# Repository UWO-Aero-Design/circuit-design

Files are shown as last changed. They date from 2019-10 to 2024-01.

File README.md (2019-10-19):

# WE Aero Design Onboard Hardware

## Goal
The hardware soloution will contain sensors that allow the team to accurately determine the height and position of the aircraft at any given moment. Also, the system should allow for communication with the ground station through an onboard radio. Logging of in-flight data and accurate GPS information will be necessary. Finally, the system must be able to control 16 individual servos or DC motors.

## Design
Below are screenshots of the current revision of the schematic and board (created in Eagle).

### Schematic
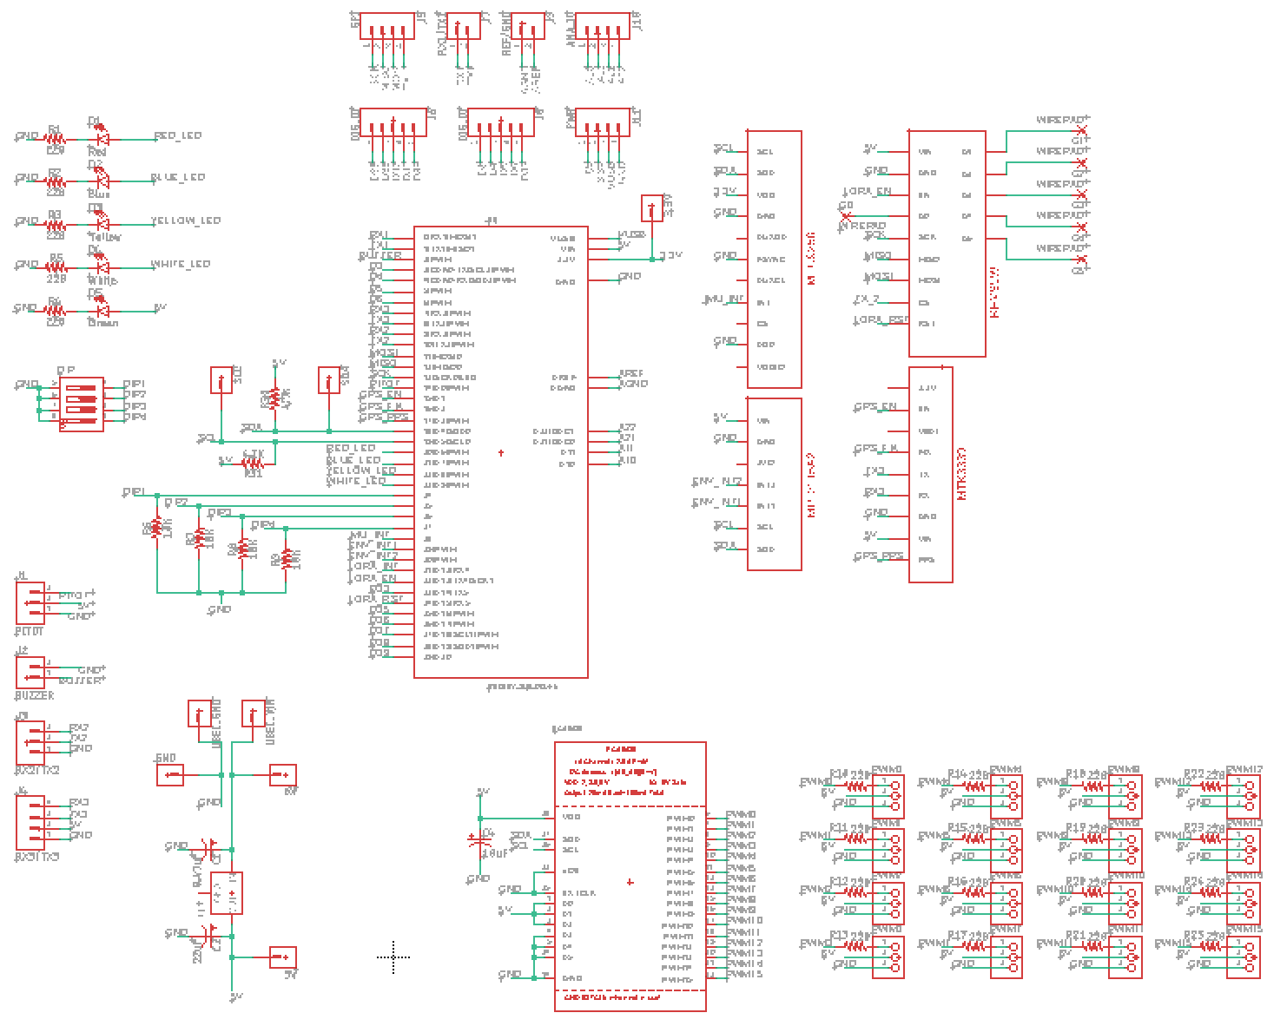
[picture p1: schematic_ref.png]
Schematic

### Board
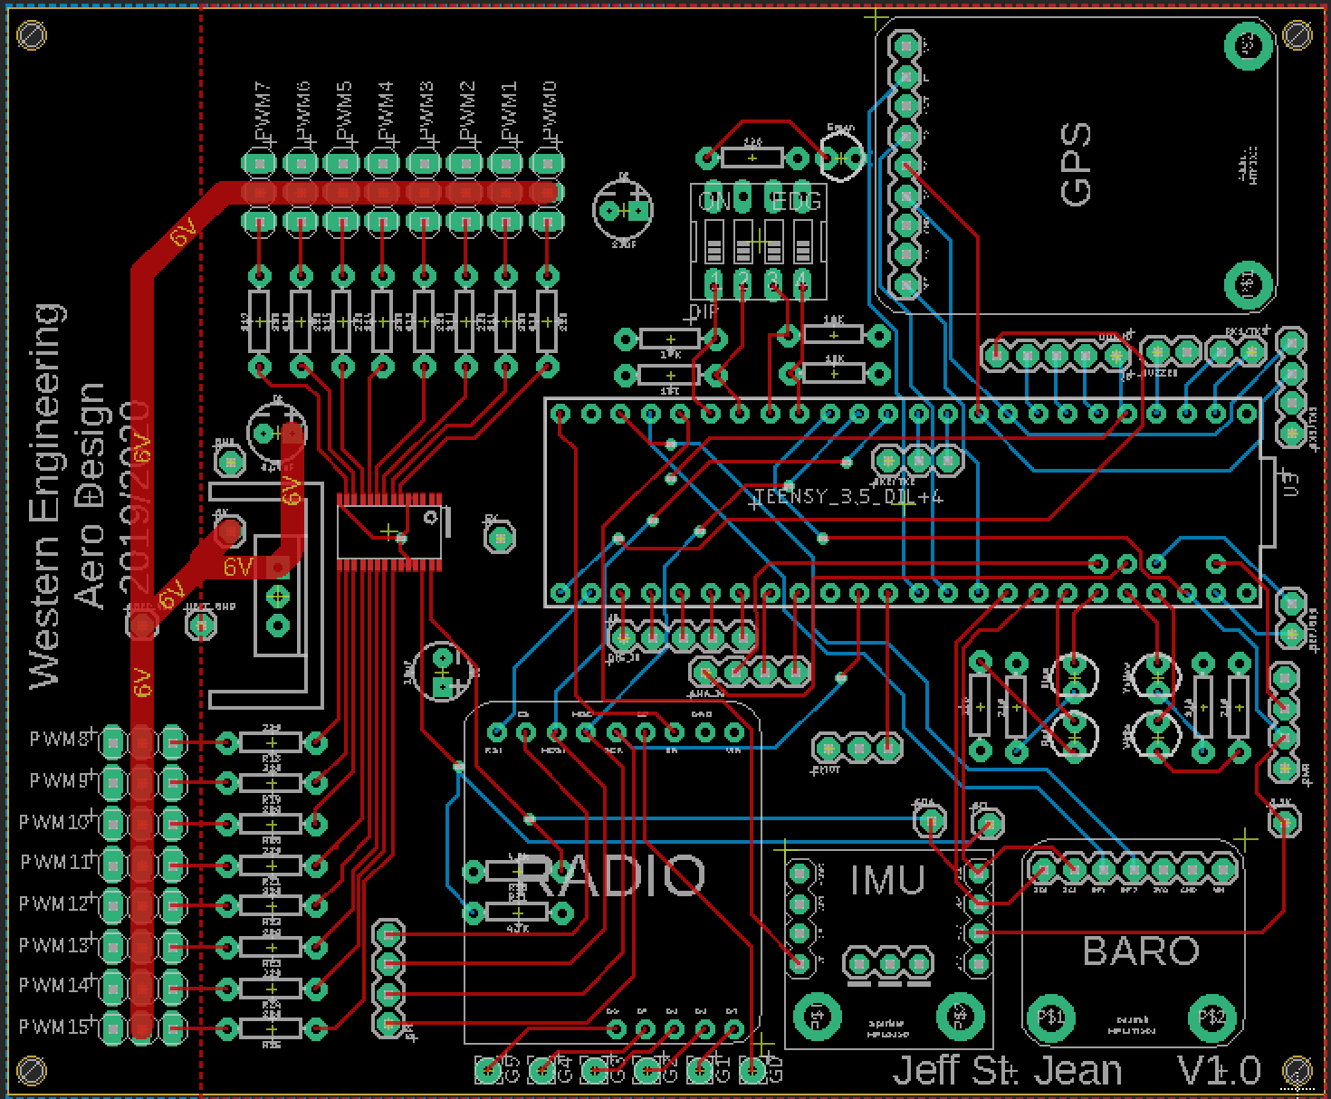
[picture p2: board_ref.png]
board


## Features
#### Radio
[RFM95W](https://www.adafruit.com/product/3072)

#### IMU
[MPU9250](https://www.sparkfun.com/products/13762)

#### Evironment Sensing
[MPL3115A2](https://www.adafruit.com/product/1893)

#### GPS
[Adafruit Ultimate GPS Breakout](https://www.adafruit.com/product/746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)

#### Servo Driver
[PCA9686](https://cdn-shop.adafruit.com/datasheets/PCA9685.pdf)

#### Power
[L7805 and L7806](https://www.mouser.ca/datasheet/2/389/l78m-974157.pdf)

## TODO
- [x] Select parts
- [x] Create schematic
- [x] Layout board
- [x] Route board
- [x] Order board
- [ ] Test board

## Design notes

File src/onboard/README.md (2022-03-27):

# WE Aero Design Onboard Hardware

## Goal
The hardware soloution will contain sensors that allow the team to accurately determine the height and position of the aircraft at any given moment. Also, the system should allow for communication with the ground station through an onboard radio. Logging of in-flight data and accurate GPS information will be necessary. Finally, the system must be able to control 16 individual servos or DC motors.

The team would also like to implement flight stabilization by activating a secondary Teensy which would control four servos attached to control surfaces: 2 aileron, 1 rudder, and 1 elevator. Activation of the secondary Teensy will be done by the Main Teensy. 

## Design
Below are screenshots of the current revision of the schematic and board of the Navigation and Main Teensy (created in Eagle).

### Schematic of Main Teensy
Schematic of Main Teensy
### Board of Main Teensy
Board of Main Teensy

### Schematic of Navigation Teensy
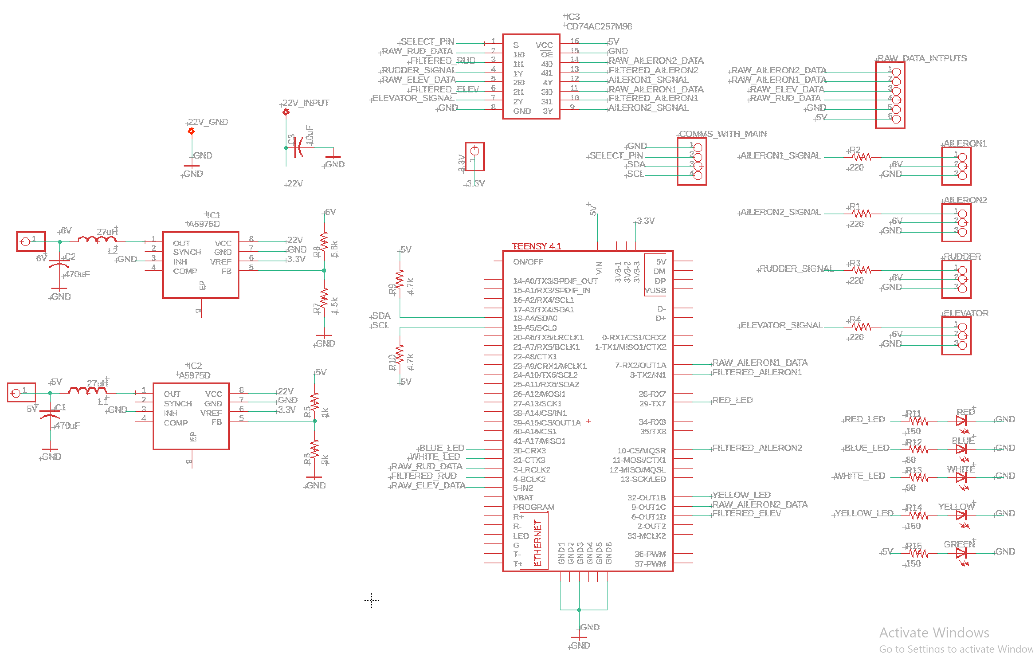
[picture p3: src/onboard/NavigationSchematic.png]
Schematic of Navigation Teensy

### Board of Navigation Teensy
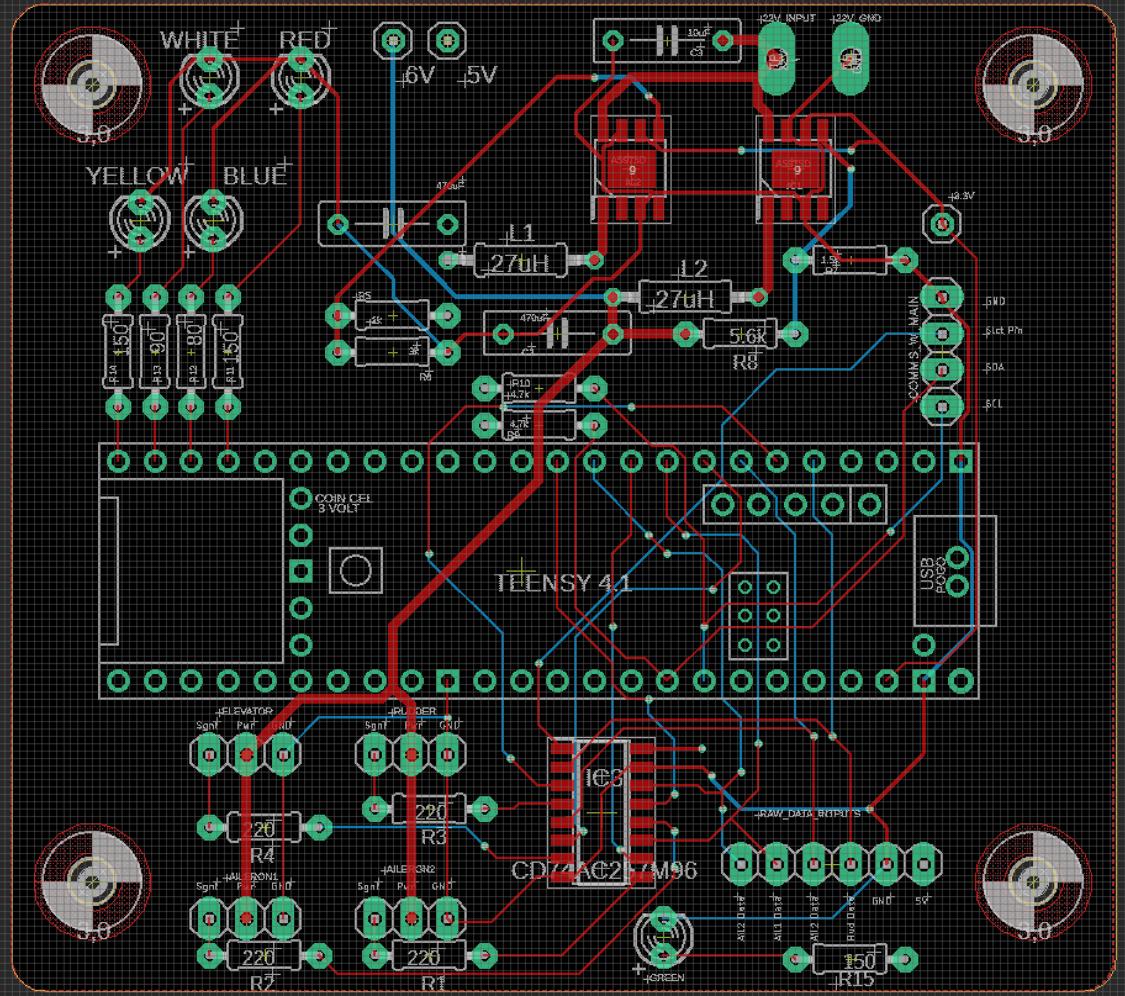
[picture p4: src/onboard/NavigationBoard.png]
Board of Navigation Teensy


## Features
#### Teensy
[Teensy 4.1](https://www.digikey.ca/en/products/detail/sparkfun-electronics/DEV-16996/13158152)

#### Radio
[RFM95W](https://www.adafruit.com/product/3072)

#### IMU
[ICM20948](https://www.digikey.ca/en/products/detail/pimoroni-ltd/PIM448/10246391)

#### Environment Sensing
[BMP280](https://www.digikey.ca/en/products/detail/adafruit-industries-llc/2651/5604371)

#### Pitot Tube
[Pitot Tube-MPXV7002DP](https://www.digikey.ca/en/products/detail/nxp-usa-inc/MPXV7002DP/1168436)

#### GPS
[Adafruit Ultimate GPS Breakout](https://www.digikey.ca/en/products/detail/adafruit-industries-llc/746/5353613)

#### Servo Driver
[PCA9685PW,112](https://www.digikey.ca/en/products/detail/nxp-usa-inc/PCA9685PW112/2034324)

#### Multiplexer
[CD74AC257M96](https://www.digikey.ca/en/products/detail/texas-instruments/CD74AC257M96/1691832)

#### Power
[A5975D](https://www.digikey.ca/en/products/detail/stmicroelectronics/A5975D/4357599)

## TODO
- [x] Select parts
- [x] Create schematic
- [x] Layout board
- [x] Route board
- [ ] Order board
- [ ] Test board

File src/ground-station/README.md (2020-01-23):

# WE Aero Design Ground Station Utility Hardware

## Goal
The hardware contains a radio and bluetooth module to allow communications between the plane's onboard system and the groundstation web server. It also contains an OLED screen to display basic information to the user as data is sent and recieved.  

## Design
Below are screenshots of the current revision of the schematic and board (created in Eagle).

### Schematic
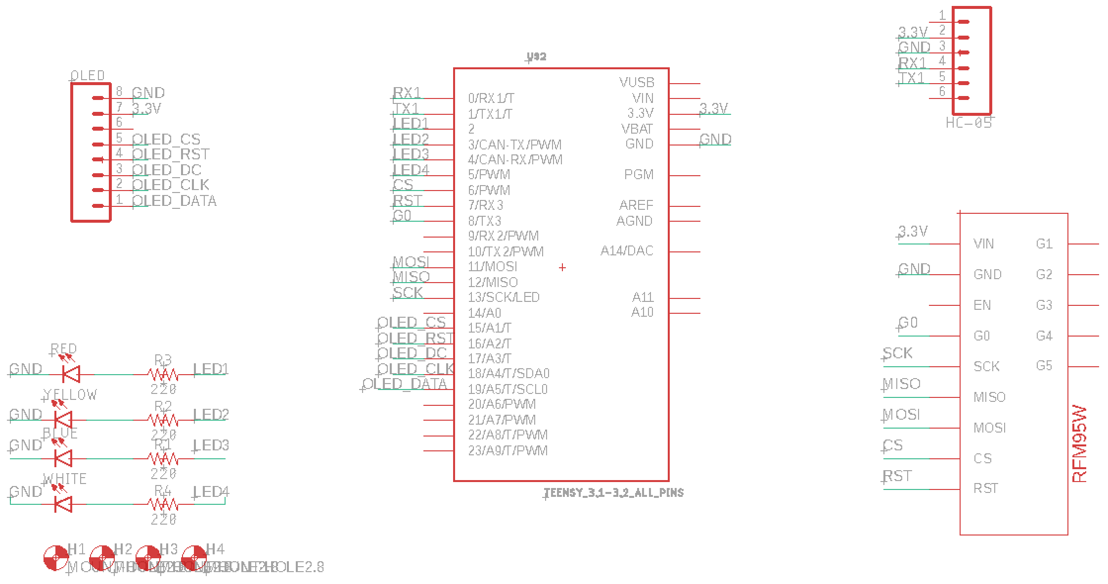
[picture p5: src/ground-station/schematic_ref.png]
Schematic

### Board
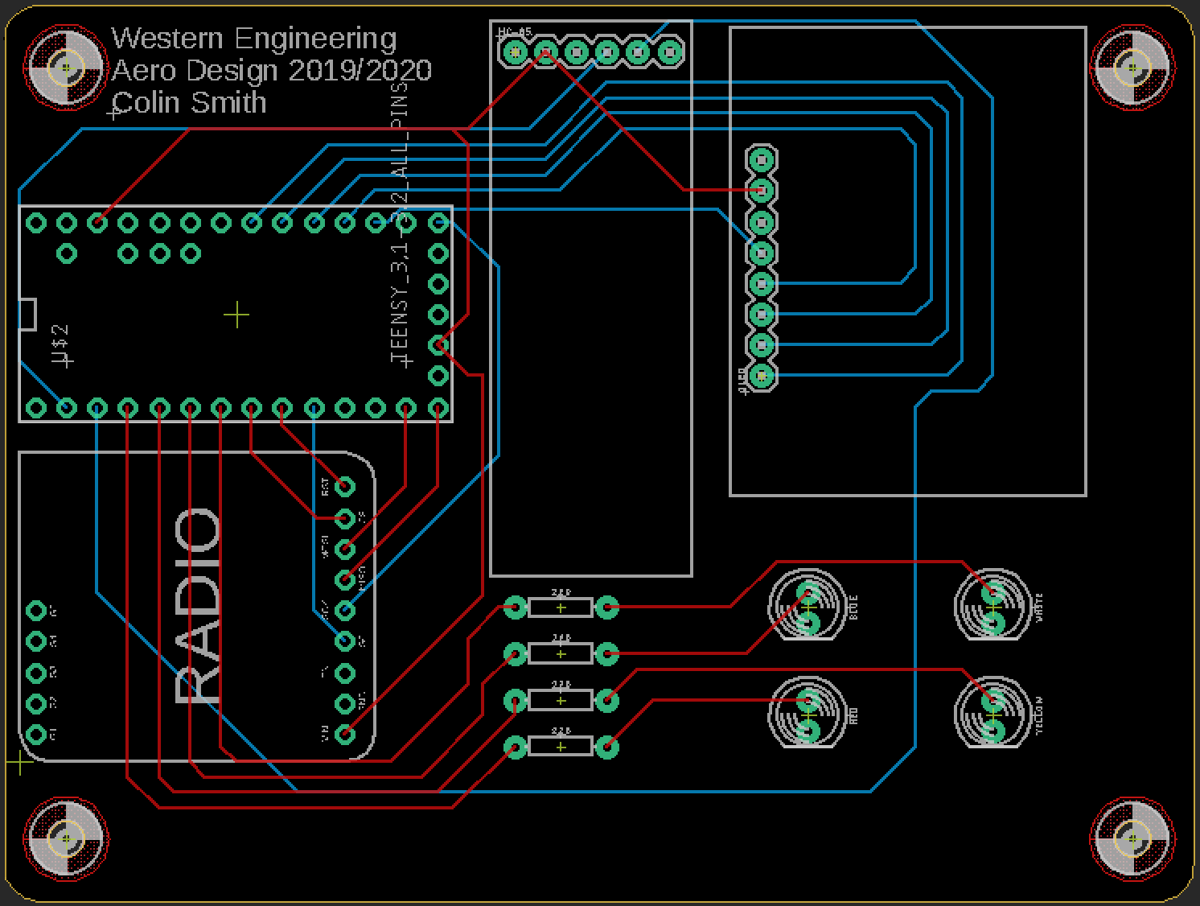
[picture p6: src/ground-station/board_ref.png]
board


## Features
#### Radio
[RFM95W](https://www.adafruit.com/product/3072)

#### Bluetooth
[HC-05](https://components101.com/wireless/hc-05-bluetooth-module)

#### OLED
[128x64 OLED](https://www.adafruit.com/product/326)

## TODO
- [x] Create schematic
- [x] Solder board
- [ ] Test Board

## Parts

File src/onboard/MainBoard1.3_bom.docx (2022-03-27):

Component | Quantity Used
Buck Converter | 3
Teensy 4.1 | 1
GPS | 1
Servo Driver | 1
Radio | 1
IMU | 1
Pitot Tube | 1
Barometer | 1
Female Header | 144
27uH Inductor | 3
470uF Capacitor | 3
10uF Capacitor | 4
1.8M Resistor | 1
430k Resistor | 1
2.2k Resistor | 5
150 Resistor | 4
80 Resistor | 1
90 Resistor | 1
5.6k Resistor | 2
1.5k Resistor | 2
1k Resistor | 1
3k Resistor | 1
10k Resistor | 2
4.7k Resistor | 2
4.3k Resistor | 1
220 Resistor | 16
ORANGE LED | 1
WHITE LED | 1
YELLOW LED | 1
RED LED | 1
BLUE | 1
GREEN LED | 1
4 DIP Switch | 1
M3 Screws | 4

Main Board:

Navigation Board:

Component | Quantity Used
Teensy 4.1 | 1
Mux | 1
Buck Converter | 2
Servo Driver | 1
27uH Inductor | 2
470uF Capacitor | 2
10uF Capacitor | 1
5.6k Resistor | 1
1.5k Resistor | 1
1k Resistor | 1
3k Resistor | 1
4.7k Resistor | 2
220 Resistor | 4
150 Resistor | 3
80 Resistor | 1
90 Resistor | 1
RED LED | 1
BLUE LED | 1
GREEN LED | 1
WHITE LED | 1
YELLOW LED | 1
Female Headers | 37
M3 Screws | 4

Component | Link | Price/1
Buck Converter | https://www.digikey.ca/en/products/detail/stmicroelectronics/A5975D/4357599 | 6.76 $
MUX | https://www.digikey.ca/en/products/detail/texas-instruments/CD74AC257M96/1691832 | 1.50 $
Teensy 4.1 | https://www.pjrc.com/store/teensy41.html | 26.85 $
GPS | https://www.digikey.ca/en/products/detail/adafruit-industries-llc/746/5353613 | 54.27 $
Radio | https://www.digikey.ca/en/products/detail/adafruit-industries-llc/3073/6005358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 | 27.10 $
Servo Driver | https://www.digikey.ca/en/products/detail/nxp-usa-inc/PCA9685PW112/2034324 | 3.47 $
IMU | https://www.digikey.ca/en/products/detail/pimoroni-ltd/PIM448/10246391 | 20.38 $
Pitot Tube | https://www.digikey.ca/en/products/detail/nxp-usa-inc/MPXV7002DP/1168436 | 27.44 $
Barometer | https://www.digikey.ca/en/products/detail/adafruit-industries-llc/2651/5604371 | 13.52 $
Header | https://www.digikey.ca/en/products/detail/sullins-connector-solutions/PPTC361LFBN-RC/810173 | 2.80 $
DIP Switches | https://www.digikey.ca/en/products/detail/grayhill-inc/76SB04T/726228 | 1.52 $
Inductors | https://www.digikey.ca/en/products/detail/epcos-tdk-electronics/B78108S1474J000/652558 | 0.50 $
Capacitors (Box) | https://www.amazon.ca/Ceramic-Capacitor-Electrolytic-Portable-Assortment/dp/B082F37H38 | 42.99 $
Resistors | https://www.digikey.ca/en/products/detail/koa-speer-electronics-inc/CF1-4CT52R104J/13537243 | 0.14 $
LEDs (Box) | https://www.amazon.ca/DiCUNO-450pcs-Colors-Emitting-Assorted/dp/B073QMYKDM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 | 19.99 $
Screws | https://www.digikey.ca/en/products/detail/keystone-electronics/29344/1532217 | 0.32 $

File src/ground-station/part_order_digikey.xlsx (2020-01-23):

Type | Qty | Device | Value | Link
Resistors | 4 | 330OHM-HORIZ-1/10W-5% | 220 | https://www.digikey.ca/product-detail/en/stackpole-electronics-inc/CF14JT220R/CF14JT220RTR-ND/1741346
Peripherals | 1 | TEENSY_3.2 | TEENSY_3.2 | https://www.digikey.ca/product-detail/en/sparkfun-electronics/DEV-13736/1568-1231-ND/5721426
 | 1 | OLED Screen | 128x64 | https://www.digikey.ca/product-detail/en/adafruit-industries-llc/326/1528-1220-ND/5353680
 | 1 | Bluetooth Module | HC-05
Connectors | 55 | Female Headers | 2.54mm Pitch | https://www.digikey.com/product-detail/en/sullins-connector-solutions/PPTC241LFBN-RC/S7022-ND/810162
 | 6 | Right-Angle Male Headers | 2.54mm Pitch | https://www.digikey.ca/product-detail/en/sullins-connector-solutions/PPPC061LGBN-RC/S5481-ND/775939
LEDs | 1 | LED3MM | Yellow LED | https://www.digikey.com/product-detail/en/lumex-opto-components-inc/SSL-LX5093YT/67-1117-ND/270915
 | 1 | LED3MM | Blue LED | https://www.digikey.com/product-detail/en/lumex-opto-components-inc/SSL-LX5093USBD/67-1751-ND/468025
 | 1 | LED3MM | Green LED | https://www.digikey.com/product-detail/en/lumex-opto-components-inc/SSL-LX5093LGT/67-1109-ND/270907
 | 1 | LED3MM | Red LED | https://www.digikey.com/product-detail/en/lumex-opto-components-inc/SSL-LX5093SRD-D/67-1648-ND/413799

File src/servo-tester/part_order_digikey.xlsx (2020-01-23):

Type | Qty | Device | Value | Link
Capacitors | 3 | 10UF-POLAR-RADIAL-2.5MM-25V-20% | 0.1uF | https://www.digikey.com/product-detail/en/vishay-bc-components/K104K15X7RF5TL2/BC1084CT-ND/286706
Resistors | 7 | 330OHM-HORIZ-1/10W-5% | 10K | https://www.digikey.ca/product-detail/en/stackpole-electronics-inc/CF14JT10K0/CF14JT10K0CT-ND/1830374
 | 3 | 330OHM-HORIZ-1/10W-5% | 220 | https://www.digikey.ca/product-detail/en/stackpole-electronics-inc/CF14JT220R/CF14JT220RTR-ND/1741346
Peripherals | 1 | TEENSY_3.2 | TEENSY_3.2 | https://www.digikey.ca/product-detail/en/sparkfun-electronics/DEV-13736/1568-1231-ND/5721426
LEDs | 1 | RGB LED 5MM | RGB LED 5MM | https://www.digikey.ca/product-detail/en/kingbright/WP154A4SUREQBFZGW/754-1492-ND/2261457
Connectors | 58 | Female Headers | 2.54mm Pitch | https://www.digikey.com/product-detail/en/sullins-connector-solutions/PPTC241LFBN-RC/S7022-ND/810162
 | 45 | Male Headers | 2.54mm Pitch | https://www.digikey.ca/product-detail/en/wurth-electronics-inc/61302411121/732-5331-ND/4846867

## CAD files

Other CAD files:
src/ground-station/dhruv_electronic design.f3z

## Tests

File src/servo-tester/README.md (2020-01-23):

# WE Aero Design Servo Tester Hardware

## Goal
To have an easy and portable way to find the bounds of the servos used to actuate the drop mechanism.

## Design
Below are screenshots of the current revision of the schematic and board (created in Eagle).

### Schematic
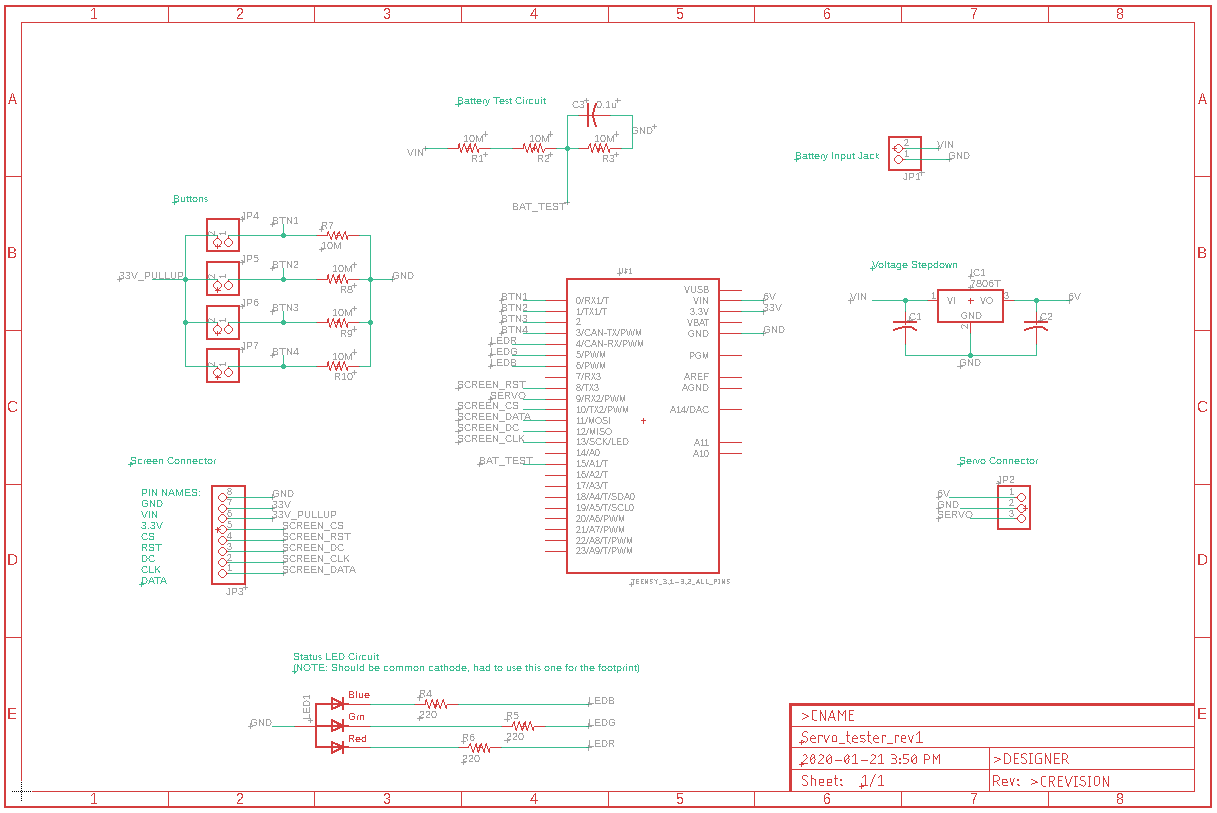
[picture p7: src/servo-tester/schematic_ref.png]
Schematic

### Board
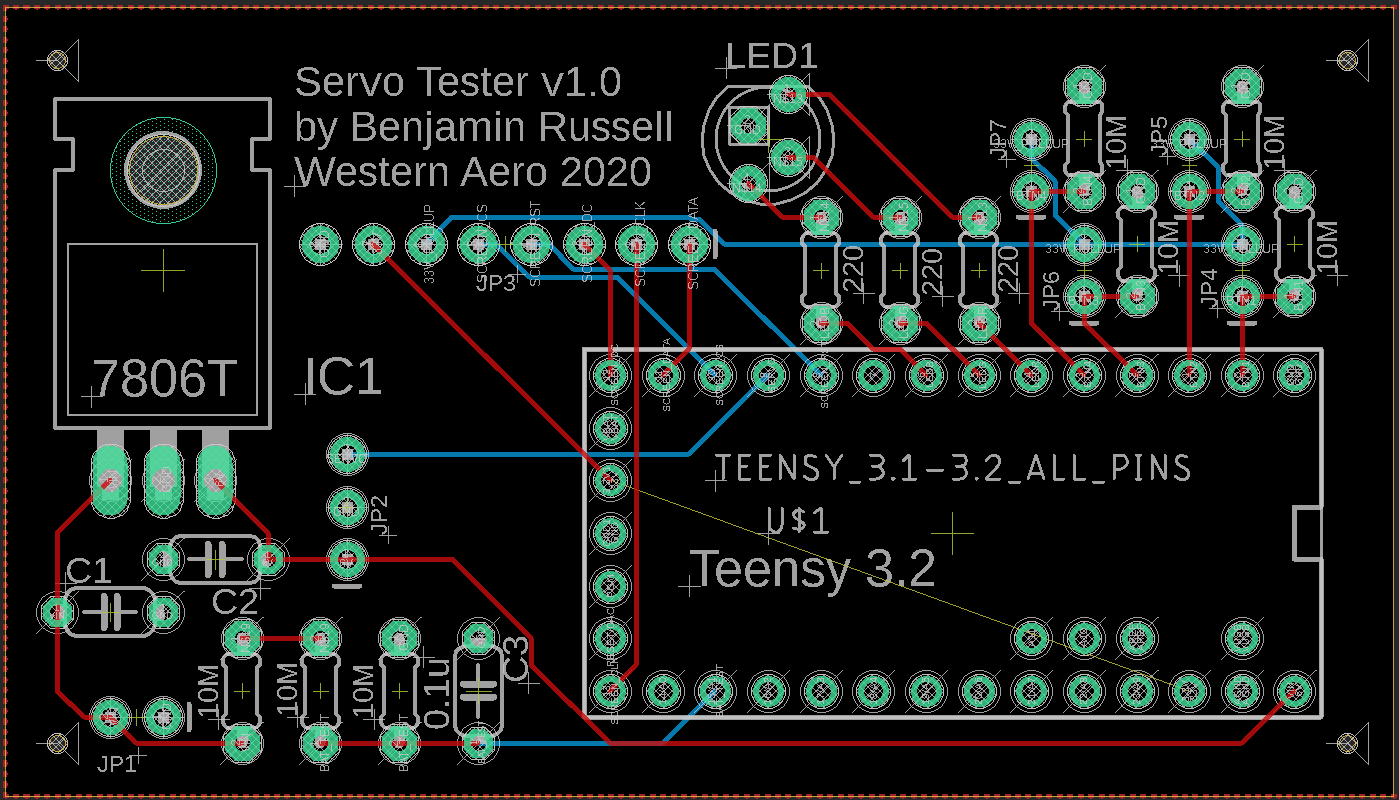
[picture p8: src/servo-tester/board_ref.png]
board


## Features
0.96" High contrast OLED display  
Battery monitor circuit  
Easily replaceable 9v battery, expected 2-4 hour life

## TODO
- [x] Create schematic
- [ ] Solder board
- [ ] Write code
- [ ] Build case

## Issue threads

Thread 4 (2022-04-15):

BMP280 silkscreen is too small

jeffstjean, 2022-04-15:

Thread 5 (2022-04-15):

Silkscreen for 27uH inductor for buck converter is too small

jeffstjean, 2022-04-15:

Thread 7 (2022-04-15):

Silkscreen for 470uF capacitor for buck converter is too small

jeffstjean, 2022-04-15:

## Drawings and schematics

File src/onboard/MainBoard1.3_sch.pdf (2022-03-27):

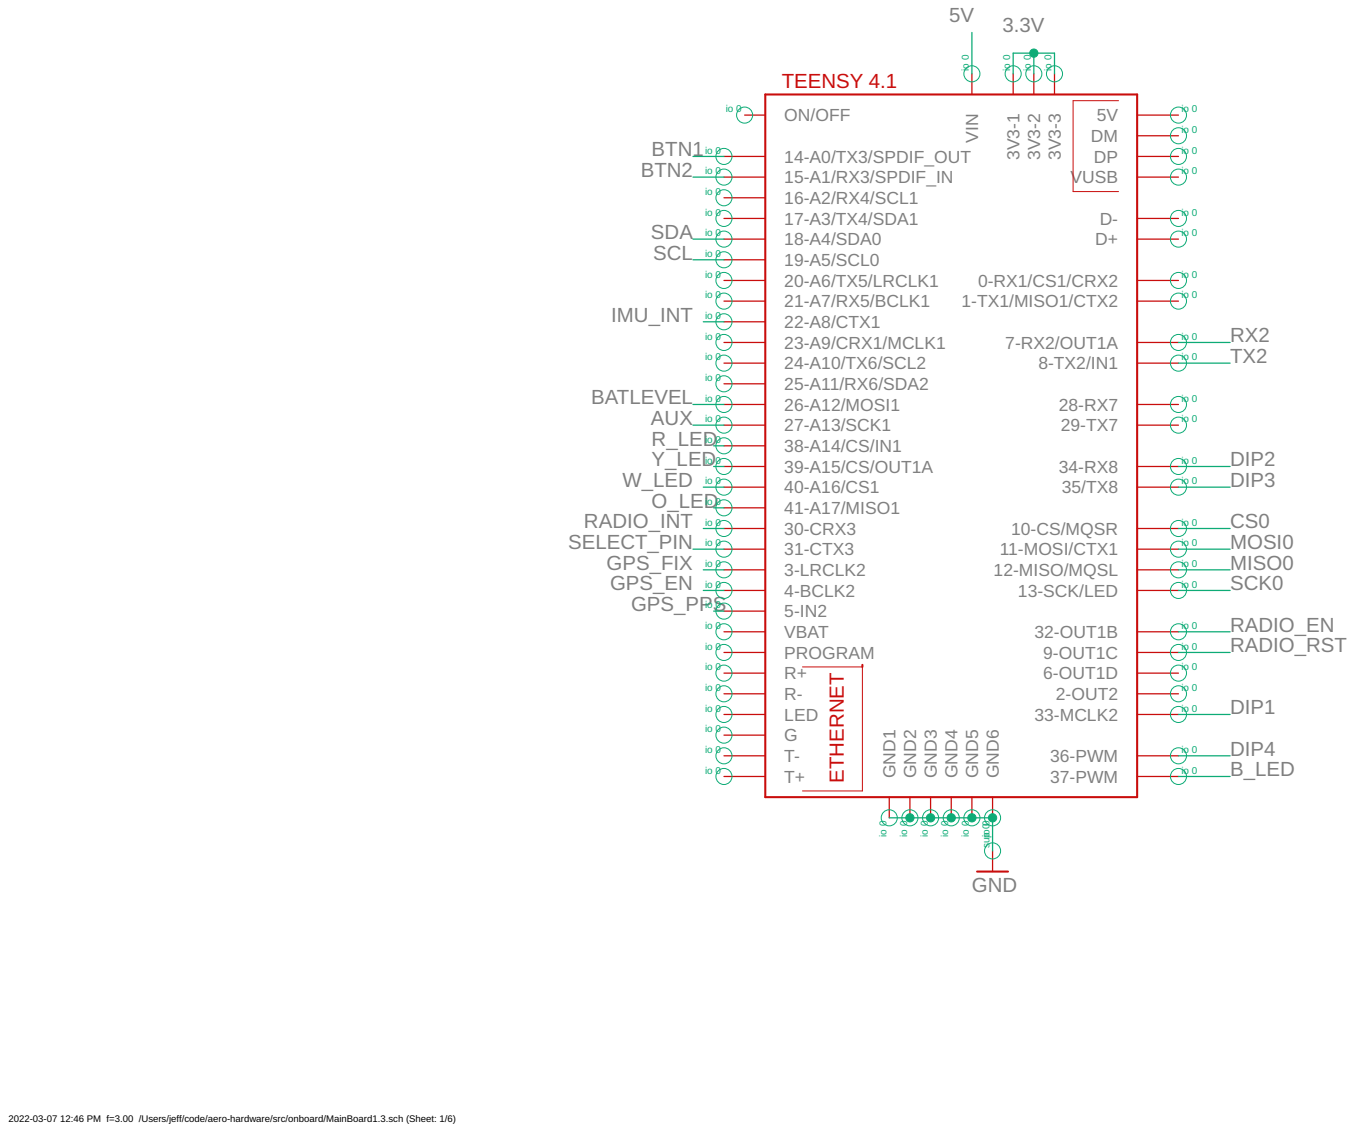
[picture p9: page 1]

2022-03-07 12:46 PM f=3.00 /Users/jeff/code/aero-hardware/src/onboard/MainBoard1.3.sch (Sheet: 1/6)

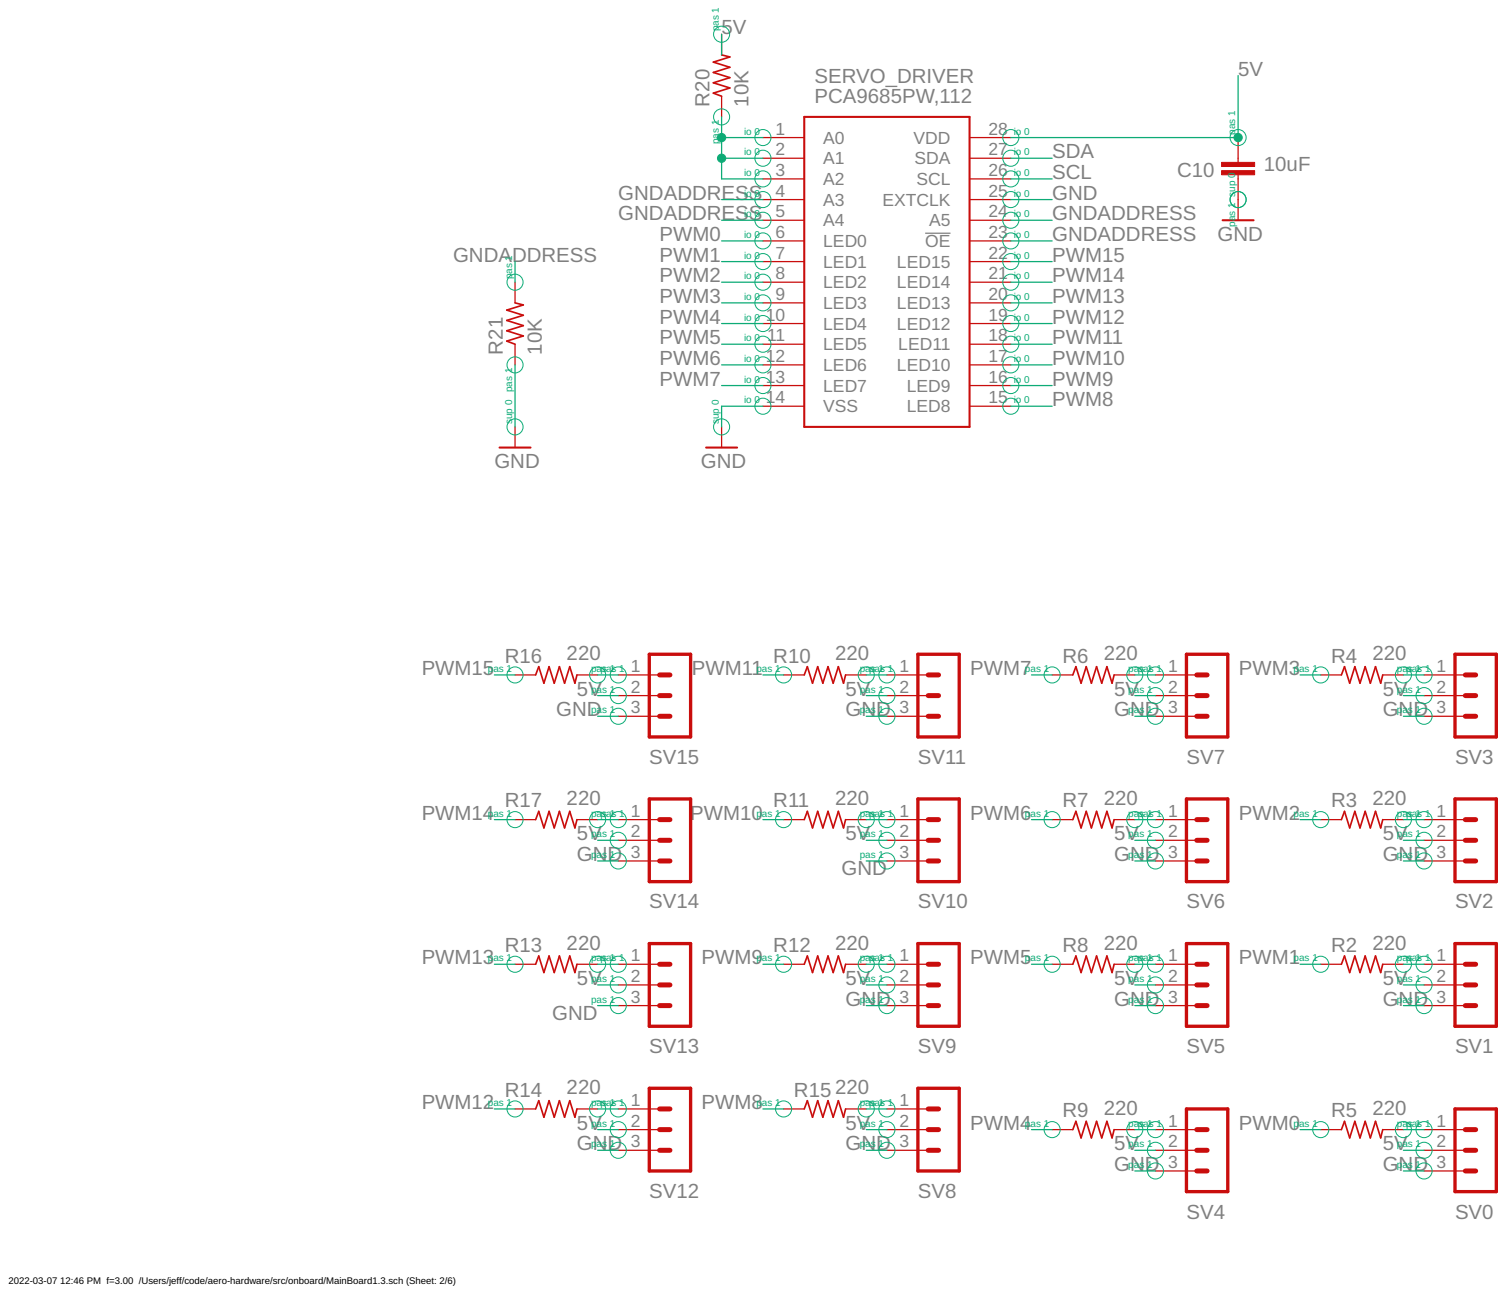
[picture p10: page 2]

2022-03-07 12:46 PM f=3.00 /Users/jeff/code/aero-hardware/src/onboard/MainBoard1.3.sch (Sheet: 2/6)

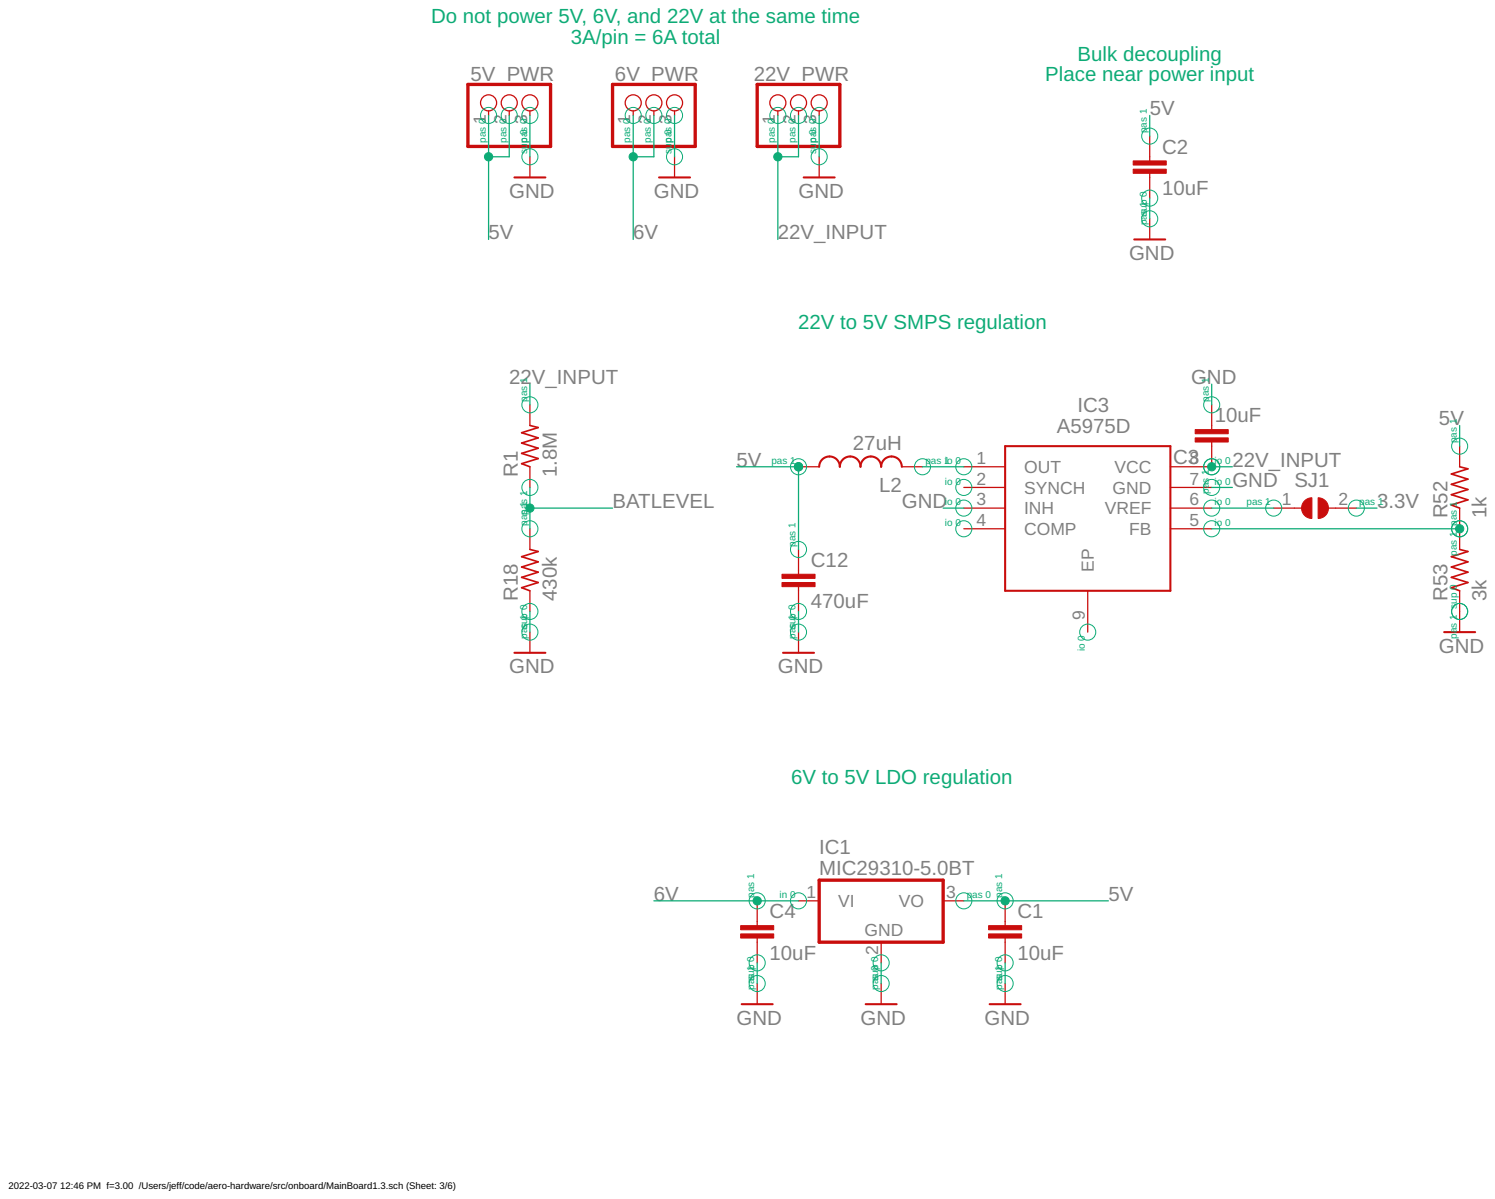
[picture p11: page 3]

Do not power 5V, 6V, and 22V at the same time

Bulk decoupling
Place near power input

2022-03-07 12:46 PM f=3.00 /Users/jeff/code/aero-hardware/src/onboard/MainBoard1.3.sch (Sheet: 3/6)

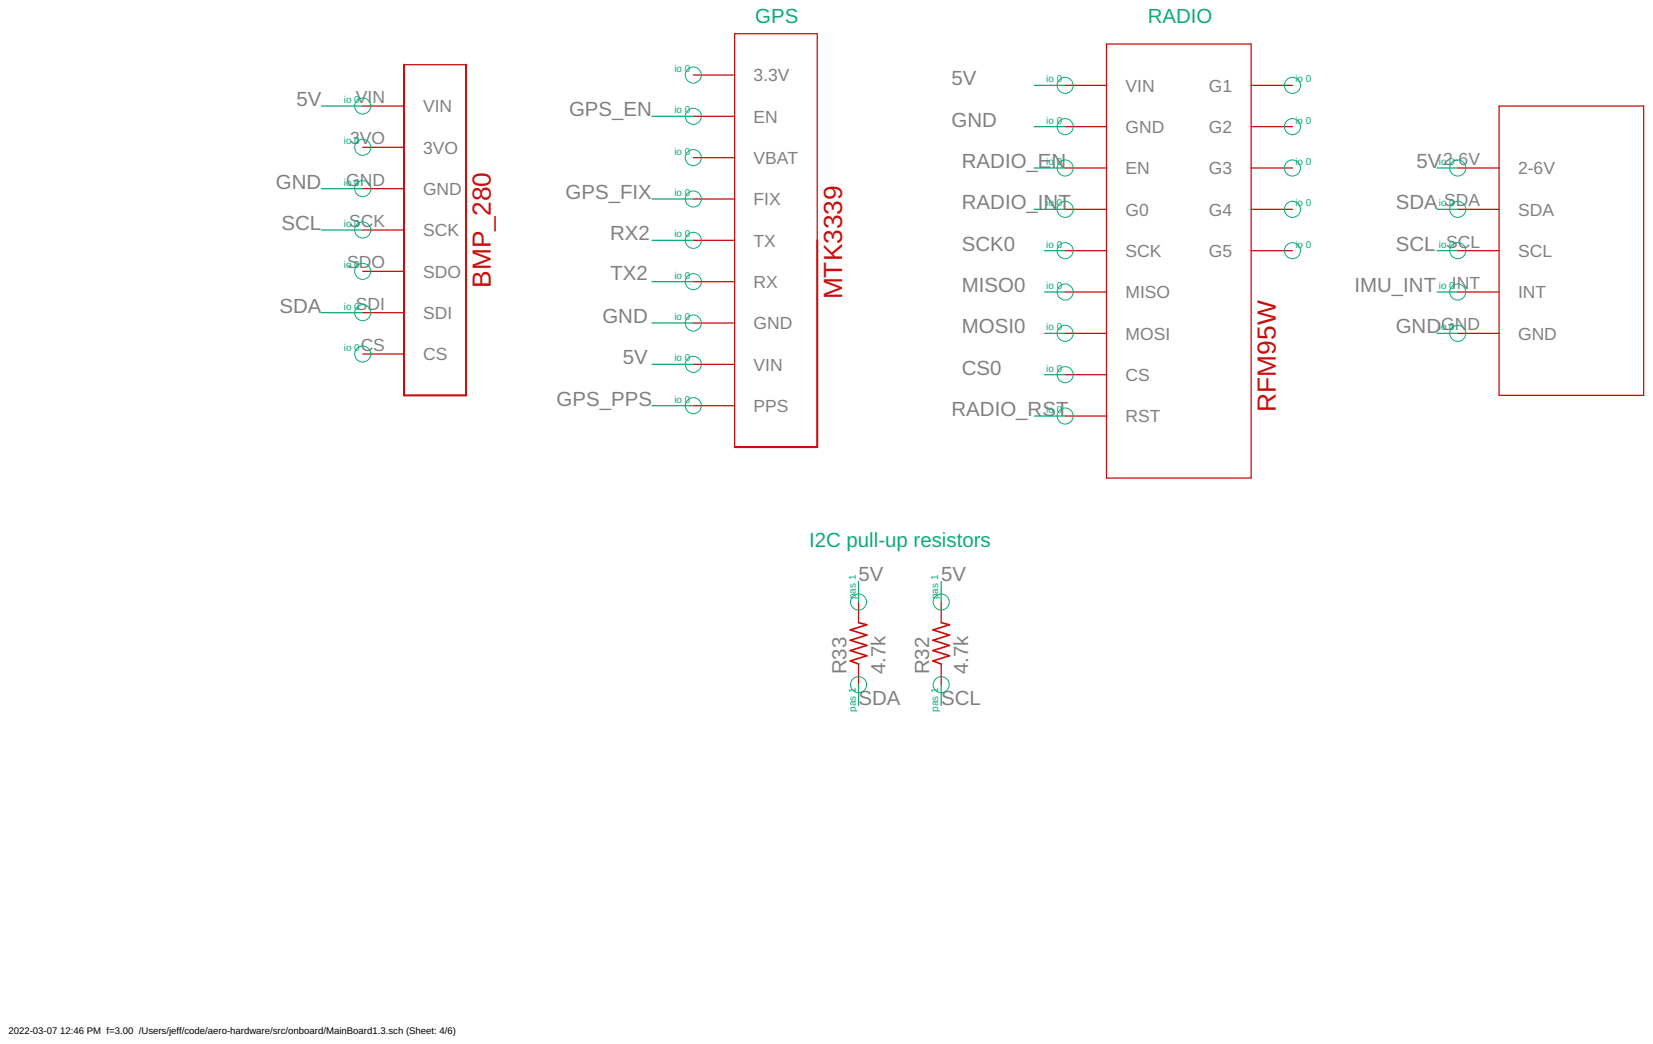
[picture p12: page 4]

2022-03-07 12:46 PM f=3.00 /Users/jeff/code/aero-hardware/src/onboard/MainBoard1.3.sch (Sheet: 4/6)

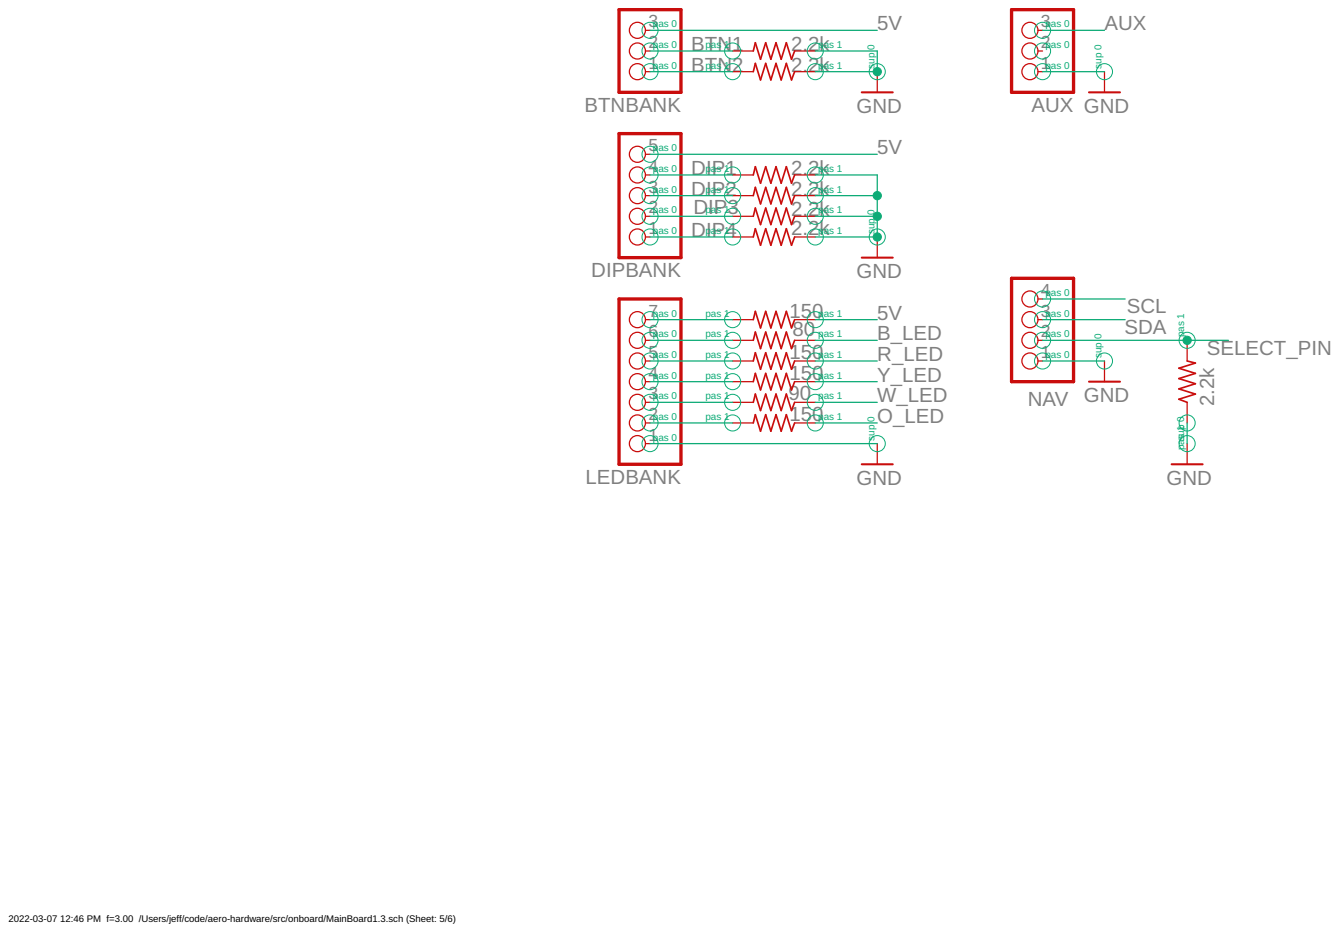
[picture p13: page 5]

2022-03-07 12:46 PM f=3.00 /Users/jeff/code/aero-hardware/src/onboard/MainBoard1.3.sch (Sheet: 5/6)

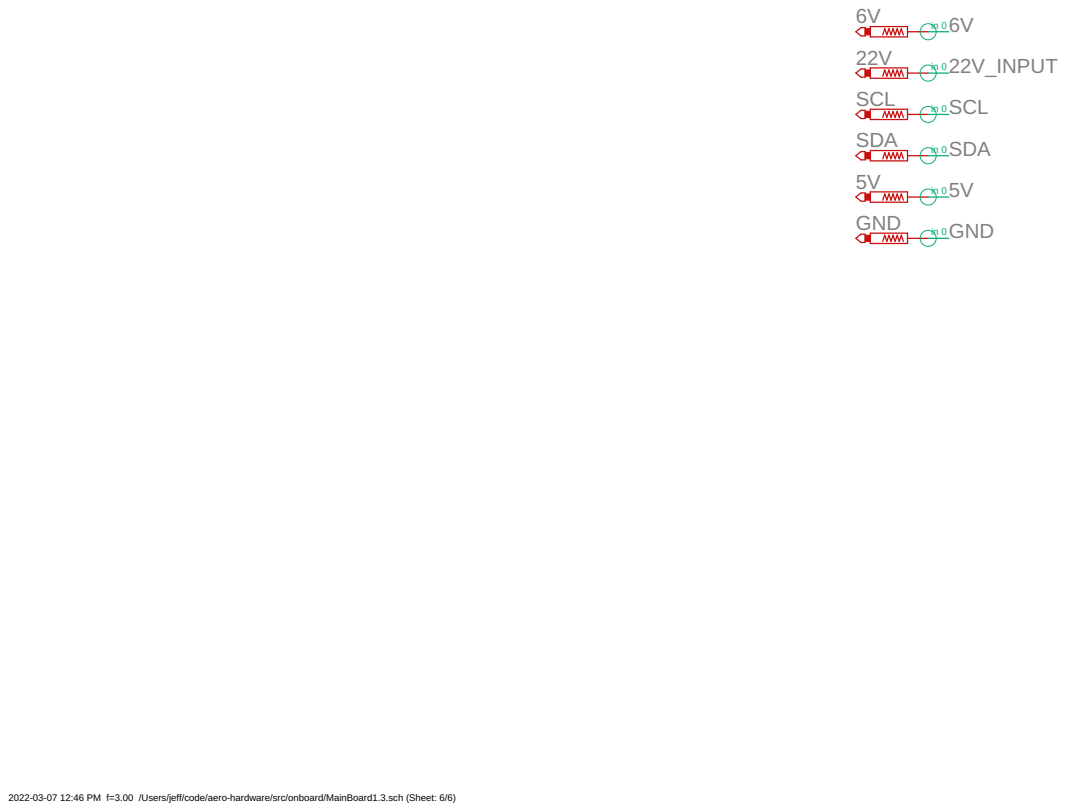
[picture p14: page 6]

2022-03-07 12:46 PM f=3.00 /Users/jeff/code/aero-hardware/src/onboard/MainBoard1.3.sch (Sheet: 6/6)

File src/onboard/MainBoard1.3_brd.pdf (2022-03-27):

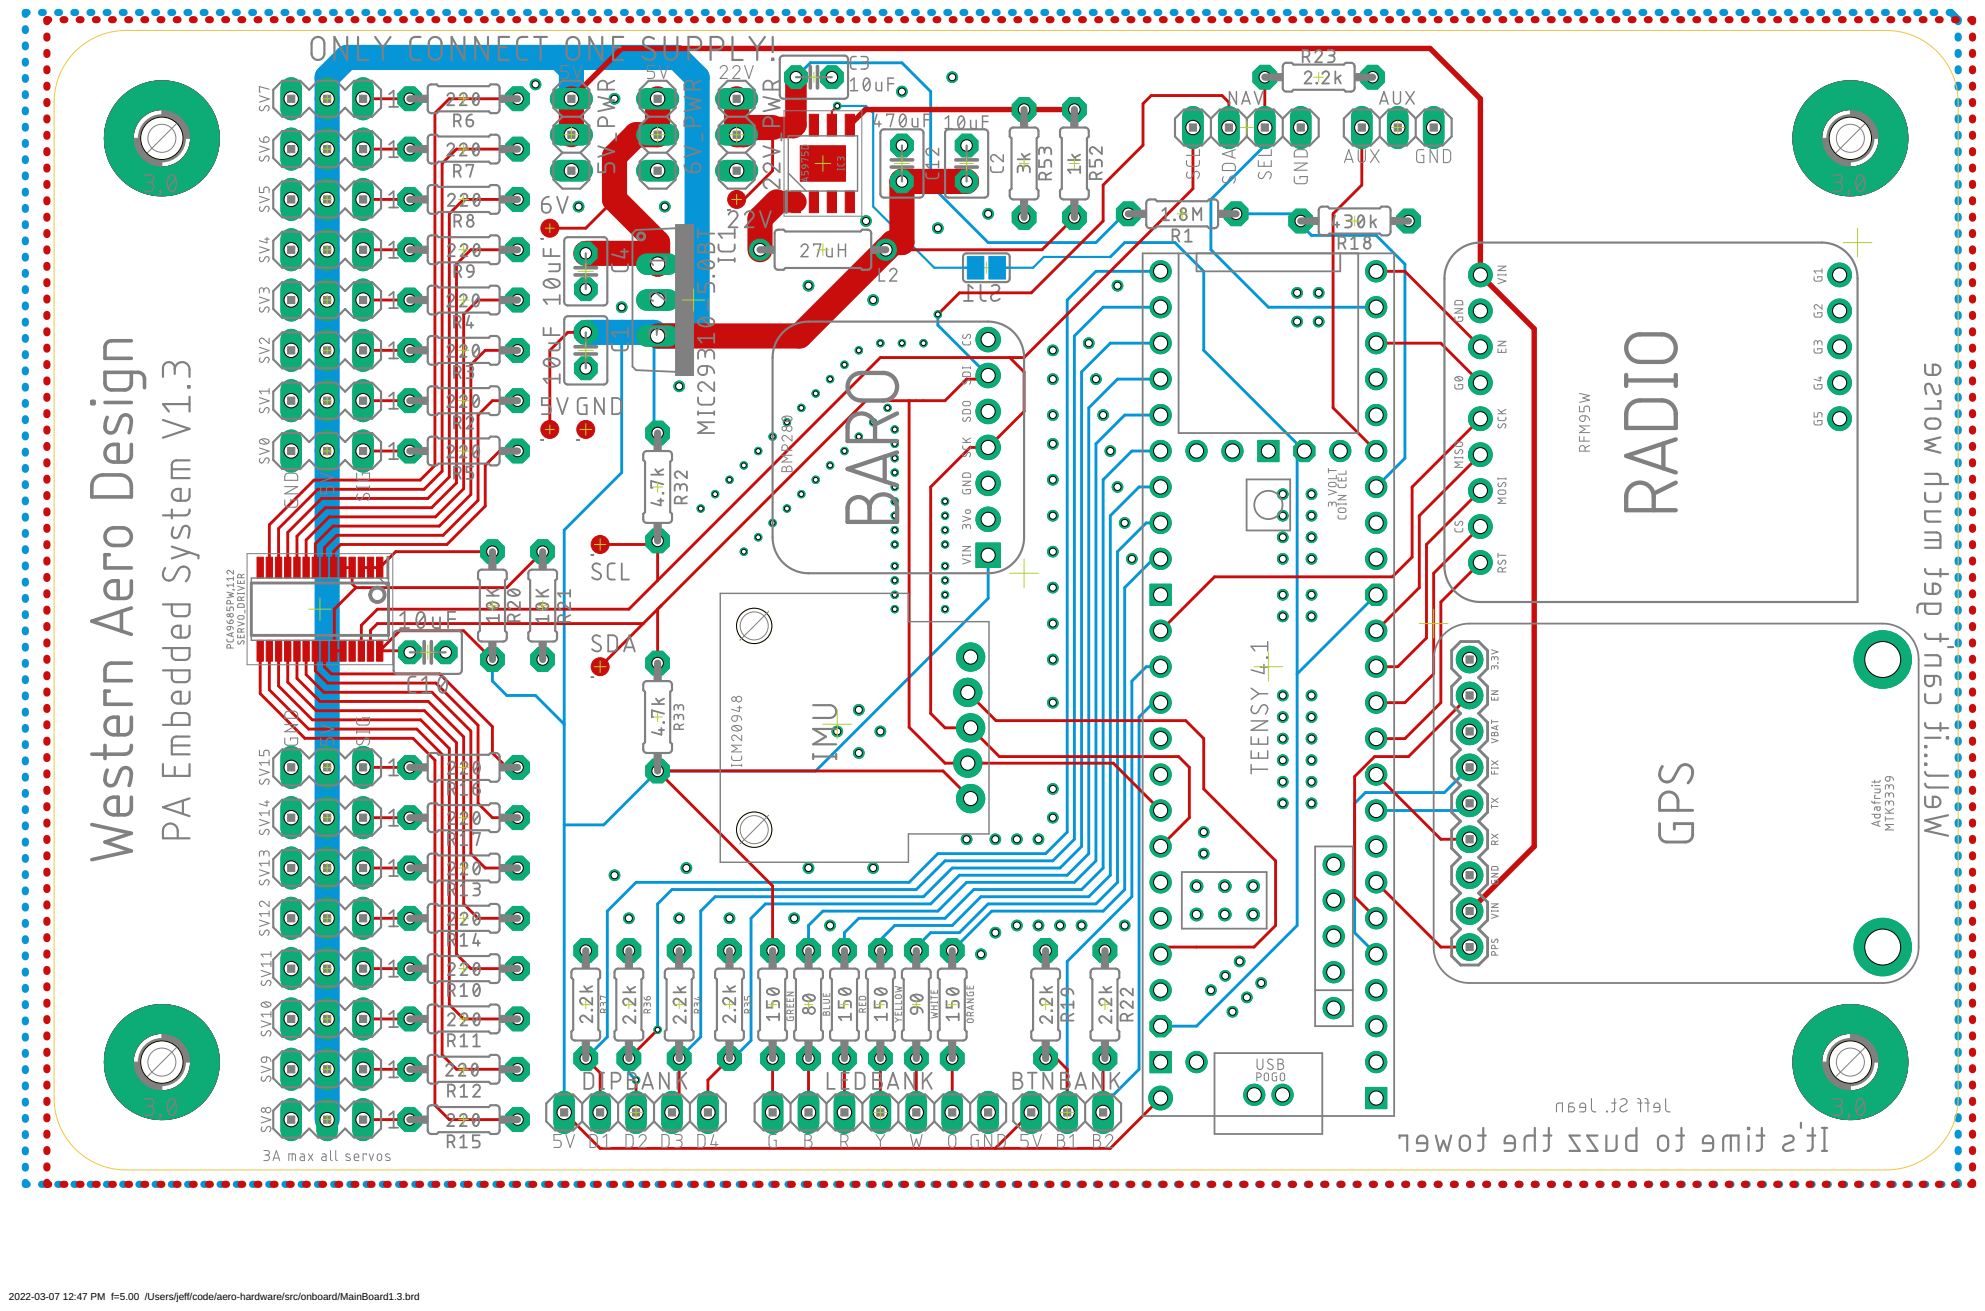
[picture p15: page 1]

2022-03-07 12:47 PM f=5.00 /Users/jeff/code/aero-hardware/src/onboard/MainBoard1.3.brd

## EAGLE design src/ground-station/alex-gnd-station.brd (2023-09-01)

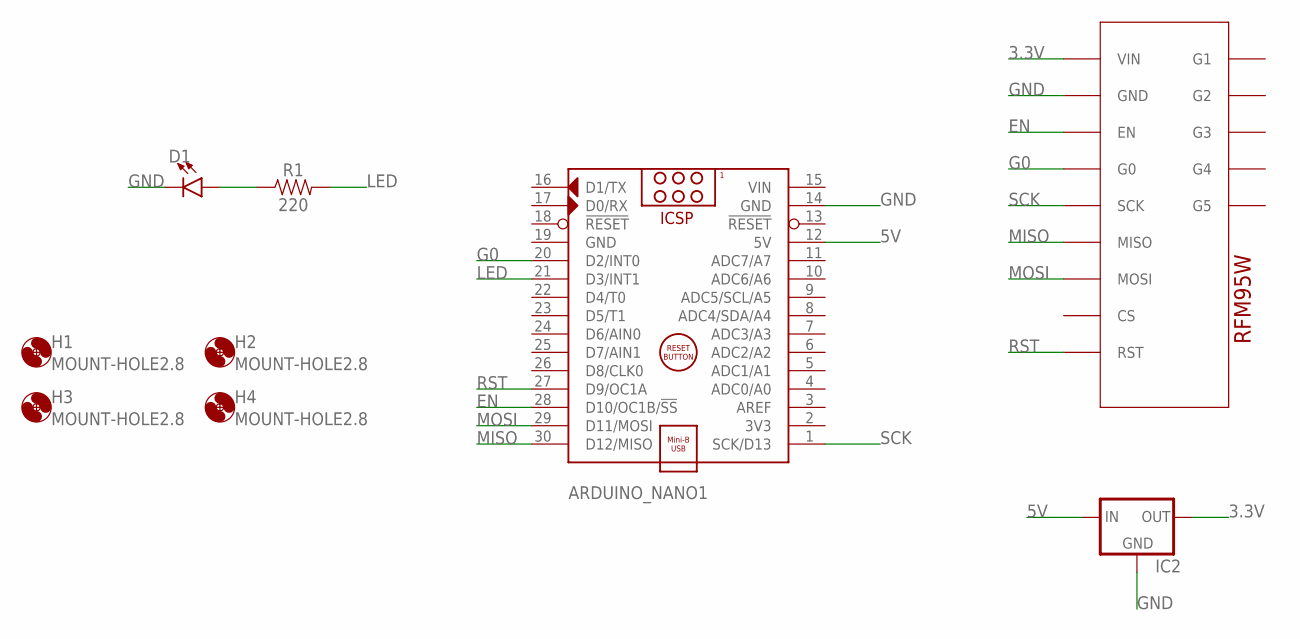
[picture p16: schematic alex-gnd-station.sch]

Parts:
ARDUINO_NANO1: ARDUINO_NANO
D1: LED5MM; LED_5MM
H1, H2, H3, H4: MOUNT-HOLE2.8; 2,8
IC2: 78XXS
R1: 220; AXIAL-0.3
U1: ADAFRUIT_RFM95W_LORA_RADIO

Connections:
3.3V: IC2.OUT, U1.1 (VIN)
5V: ARDUINO_NANO1.12 (5V), IC2.IN
EN: ARDUINO_NANO1.28 (D10/OC1B/!SS), U1.3 (EN)
G0: ARDUINO_NANO1.20 (D2/INT0), U1.4 (G0)
GND: ARDUINO_NANO1.14 (GND), ARDUINO_NANO1.19 (GND), D1.K (C), IC2.GND, U1.2 (GND)
LED: ARDUINO_NANO1.21 (D3/INT1), R1.P$2 (2)
MISO: ARDUINO_NANO1.30 (D12/MISO), U1.6 (MISO)
MOSI: ARDUINO_NANO1.29 (D11/MOSI), U1.7 (MOSI)
unnamed: D1.A, R1.P$1 (1)
RST: ARDUINO_NANO1.27 (D9/OC1A), U1.9 (RST)
SCK: ARDUINO_NANO1.1 (SCK/D13), U1.5 (SCK)
VIN: ARDUINO_NANO1.15 (VIN)

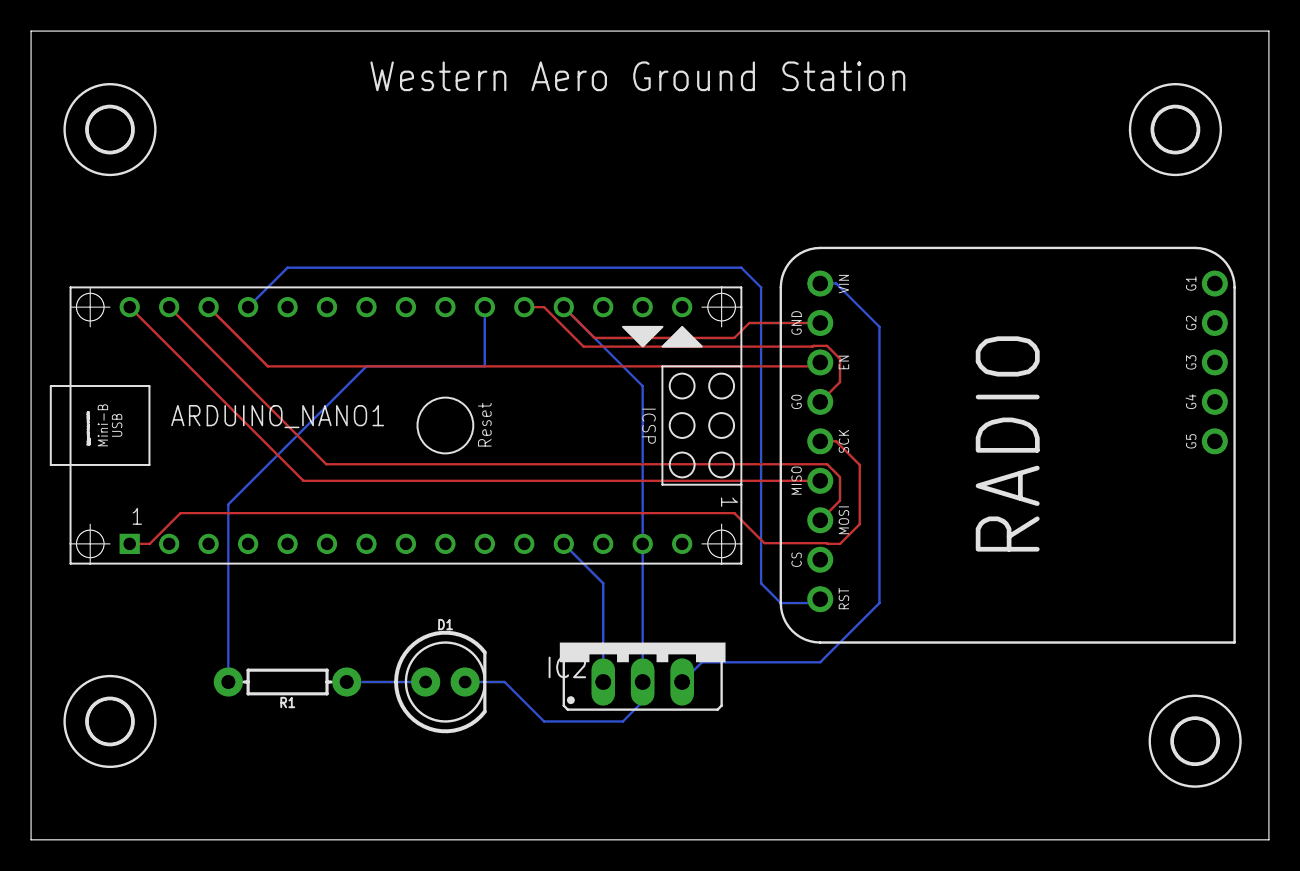
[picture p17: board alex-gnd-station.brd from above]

Board: 2 copper layers, 79.7 x 52.1 mm, 9 parts (0 on the bottom side), 11 nets.

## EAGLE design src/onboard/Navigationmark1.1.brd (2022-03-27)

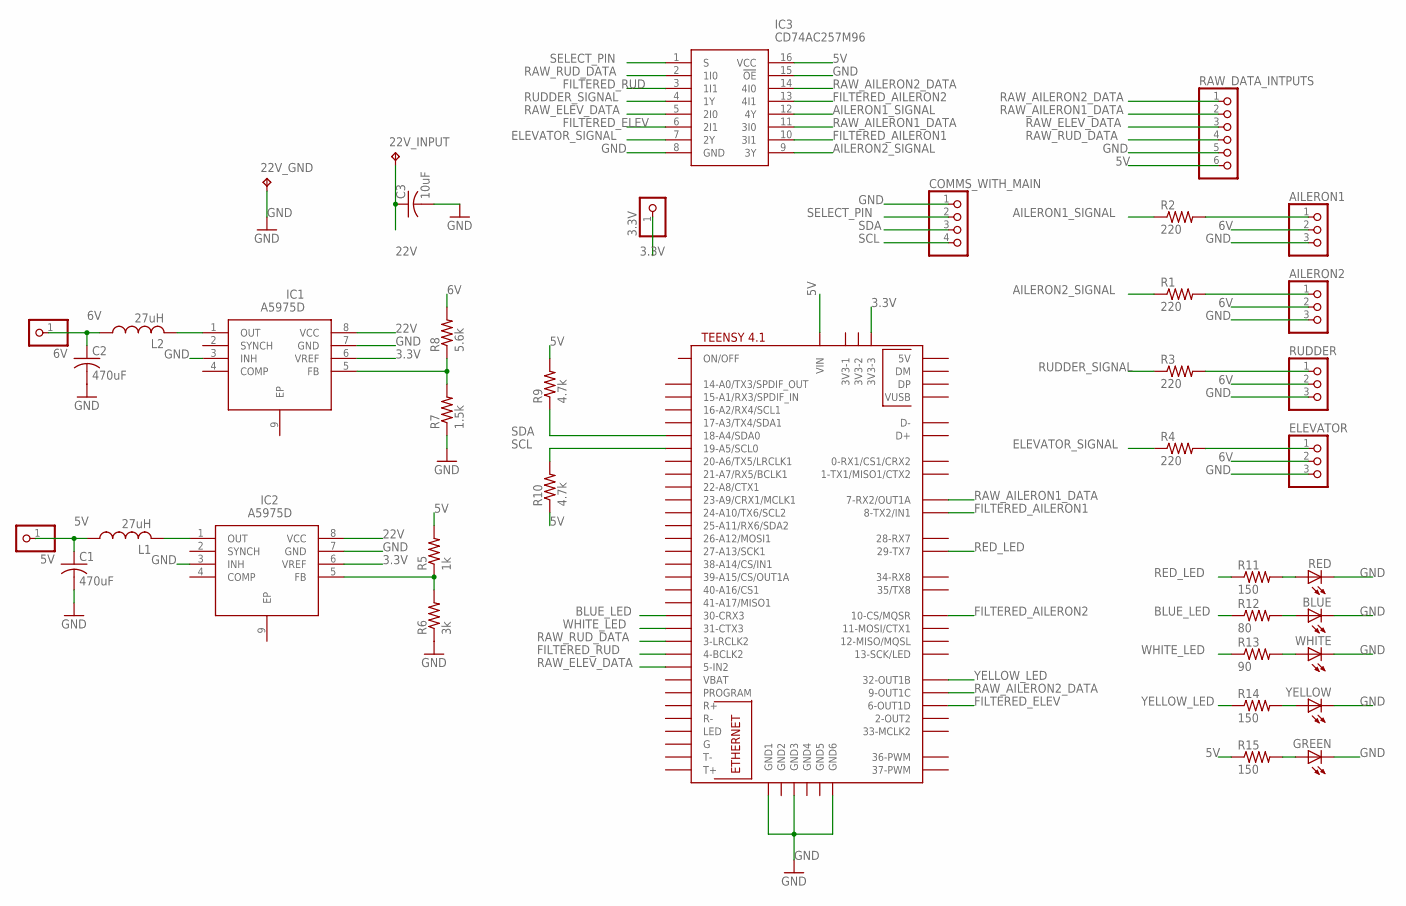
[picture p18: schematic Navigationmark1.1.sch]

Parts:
3.3V, 5V, 6V: PINHD-1X1; 1X01
22V_GND, 22V_INPUT: TPPAD1-17Y; P1-17Y
AILERON1, AILERON2: PINHD-1X3; 1X03
BLUE: LED3MM
C1, C2: 470uF; C075-032X103
C3: 10uF; C075-032X103
COMMS_WITH_MAIN: PINHD-1X4; 1X04
ELEVATOR: PINHD-1X3; 1X03
GREEN: LED3MM
IC1, IC2: A5975D; SOIC127P600X170-9N
IC3: CD74AC257M96; SOIC127P600X175-16N
L1, L2: 27uH; 0207/10
R1, R2, R3, R4: 220; 0204/7
R5: 1k; 0204/7
R6: 3k; 0204/7
R7: 1.5k; 0204/7
R8: 5.6k; 0204/7
R9, R10: 4.7k; 0204/7
R11, R14, R15: 150; 0204/7
R12: 80; 0204/7
R13: 90; 0204/7
RAW_DATA_INTPUTS: PINHD-1X6; 1X06
RED: LED3MM
RUDDER: PINHD-1X3; 1X03
U$1: TEENSY41
WHITE: LED3MM
YELLOW: LED3MM

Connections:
3.3V: 3.3V.1, IC1.6 (VREF), IC2.6 (VREF), U$1.3V3-3
5V: 5V.1, C1.1, IC3.16 (VCC), L1.1, R5.2, R9.2, R10.1, R15.1, RAW_DATA_INTPUTS.6, U$1.VIN
6V: 6V.1, AILERON1.2, AILERON2.2, C2.1, ELEVATOR.2, L2.1, R8.2, RUDDER.2
22V: 22V_INPUT.TP, C3.1, IC1.8 (VCC), IC2.8 (VCC)
AILERON1_SIGNAL: IC3.12 (4Y), R2.1
AILERON2_SIGNAL: IC3.9 (3Y), R1.1
BLUE_LED: R12.1, U$1.30-CRX3
ELEVATOR_SIGNAL: IC3.7 (2Y), R4.1
FILTERED_AILERON1: IC3.10 (3I1), U$1.8-TX2/IN1
FILTERED_AILERON2: IC3.13 (4I1), U$1.10-CS\MQSR (10-CS/MQSR)
FILTERED_ELEV: IC3.6 (2I1), U$1.6-OUT1D
FILTERED_RUD: IC3.3 (1I1), U$1.4-BCLK2
GND: 22V_GND.TP, AILERON1.3, AILERON2.3, BLUE.K (C), C1.2, C2.2, C3.2, COMMS_WITH_MAIN.1, ELEVATOR.3, GREEN.K (C), IC1.3 (INH), IC1.7 (GND), IC2.3 (INH), IC2.7 (GND), IC3.8 (GND), IC3.15 (!OE), R6.1, R7.1, RAW_DATA_INTPUTS.5, RED.K (C), RUDDER.3, U$1.GND1, U$1.GND3, U$1.GND6, WHITE.K (C), YELLOW.K (C); also elsewhere on the board
unnamed: AILERON1.1, R2.2
unnamed: GREEN.A, R15.2
unnamed: AILERON2.1, R1.2
unnamed: R3.2, RUDDER.1
unnamed: IC1.1 (OUT), L2.2
unnamed: R11.2, RED.A
unnamed: ELEVATOR.1, R4.2
unnamed: IC2.1 (OUT), L1.2
unnamed: IC2.5 (FB), R5.1, R6.2
unnamed: IC1.5 (FB), R7.2, R8.1
unnamed: BLUE.A, R12.2
unnamed: R13.2, WHITE.A
unnamed: R14.2, YELLOW.A
RAW_AILERON1_DATA: IC3.11 (3I0), RAW_DATA_INTPUTS.2, U$1.7-RX2/OUT1A
RAW_AILERON2_DATA: IC3.14 (4I0), RAW_DATA_INTPUTS.1, U$1.9-OUT1C
RAW_ELEV_DATA: IC3.5 (2I0), RAW_DATA_INTPUTS.3, U$1.5-IN2
RAW_RUD_DATA: IC3.2 (1I0), RAW_DATA_INTPUTS.4, U$1.3-LRCLK2
RED_LED: R11.1, U$1.29-TX7
RUDDER_SIGNAL: IC3.4 (1Y), R3.1
SCL: COMMS_WITH_MAIN.4, R10.2, U$1.19-A5/SCL0; also elsewhere on the board
SDA: COMMS_WITH_MAIN.3, R9.1, U$1.18-A4/SDA0; also elsewhere on the board
SELECT_PIN: COMMS_WITH_MAIN.2, IC3.1 (S); also elsewhere on the board
WHITE_LED: R13.1, U$1.31-CTX3
YELLOW_LED: R14.1, U$1.32-OUT1B

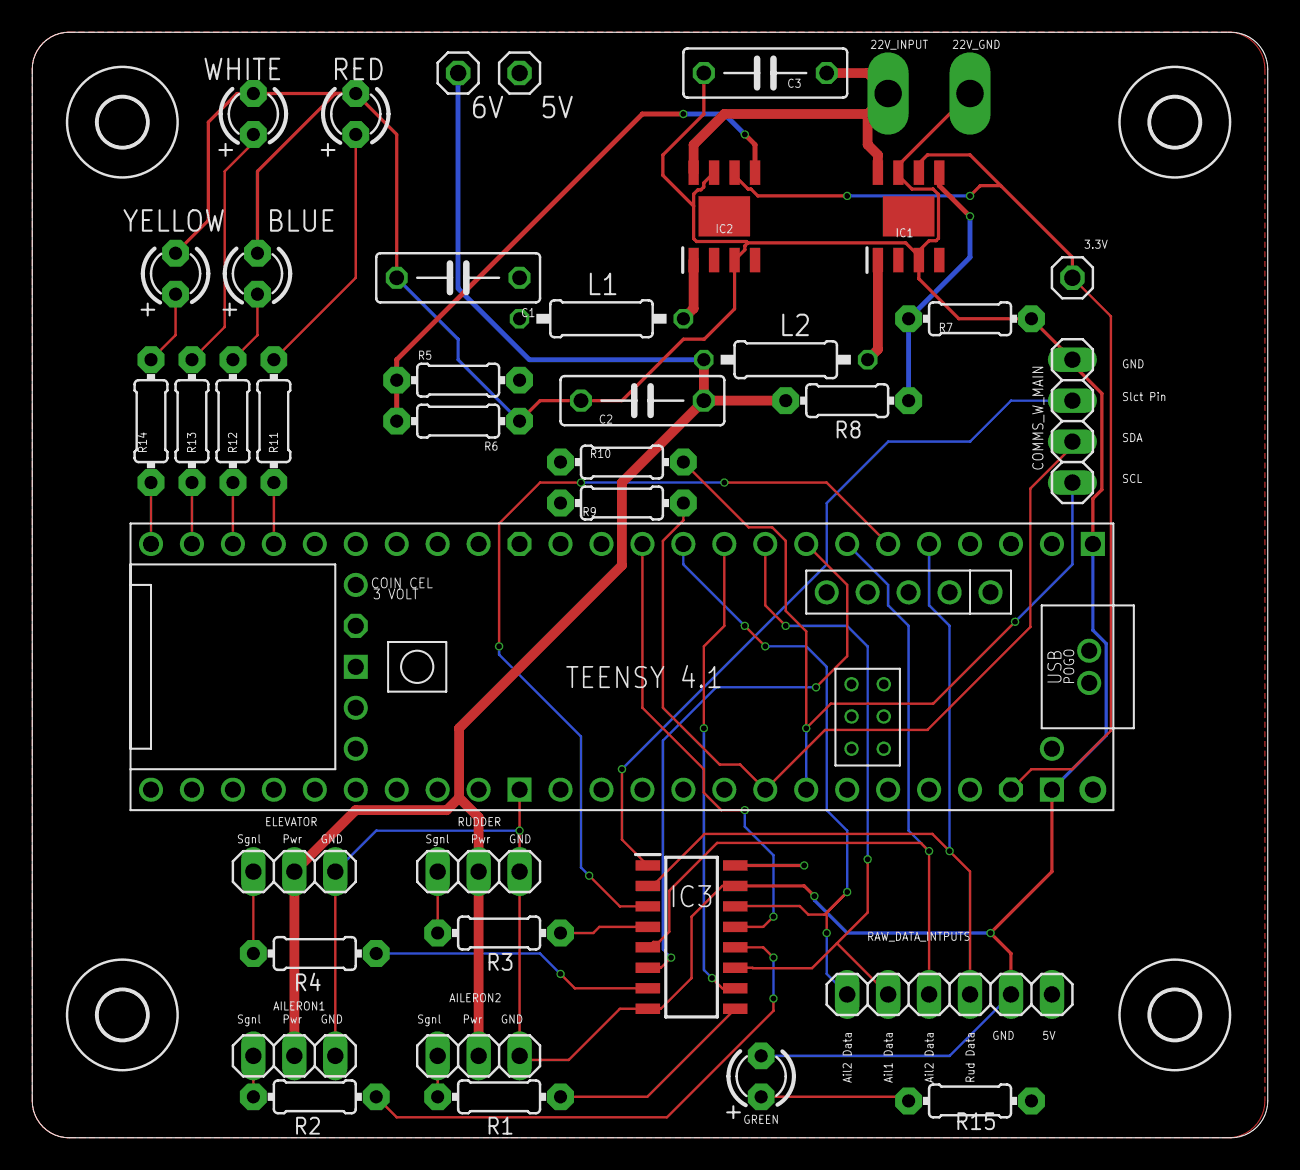
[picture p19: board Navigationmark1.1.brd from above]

Board: 2 copper layers, 76.6 x 68.6 mm, 44 parts (0 on the bottom side), 37 nets.

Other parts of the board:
COMMS_W_MAIN: 1X04
E$1, E$2, E$3, E$4: 3,0

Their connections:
GND: COMMS_W_MAIN.1; also elsewhere on the board
SCL: COMMS_W_MAIN.4; also elsewhere on the board
SDA: COMMS_W_MAIN.3; also elsewhere on the board
SELECT_PIN: COMMS_W_MAIN.2; also elsewhere on the board

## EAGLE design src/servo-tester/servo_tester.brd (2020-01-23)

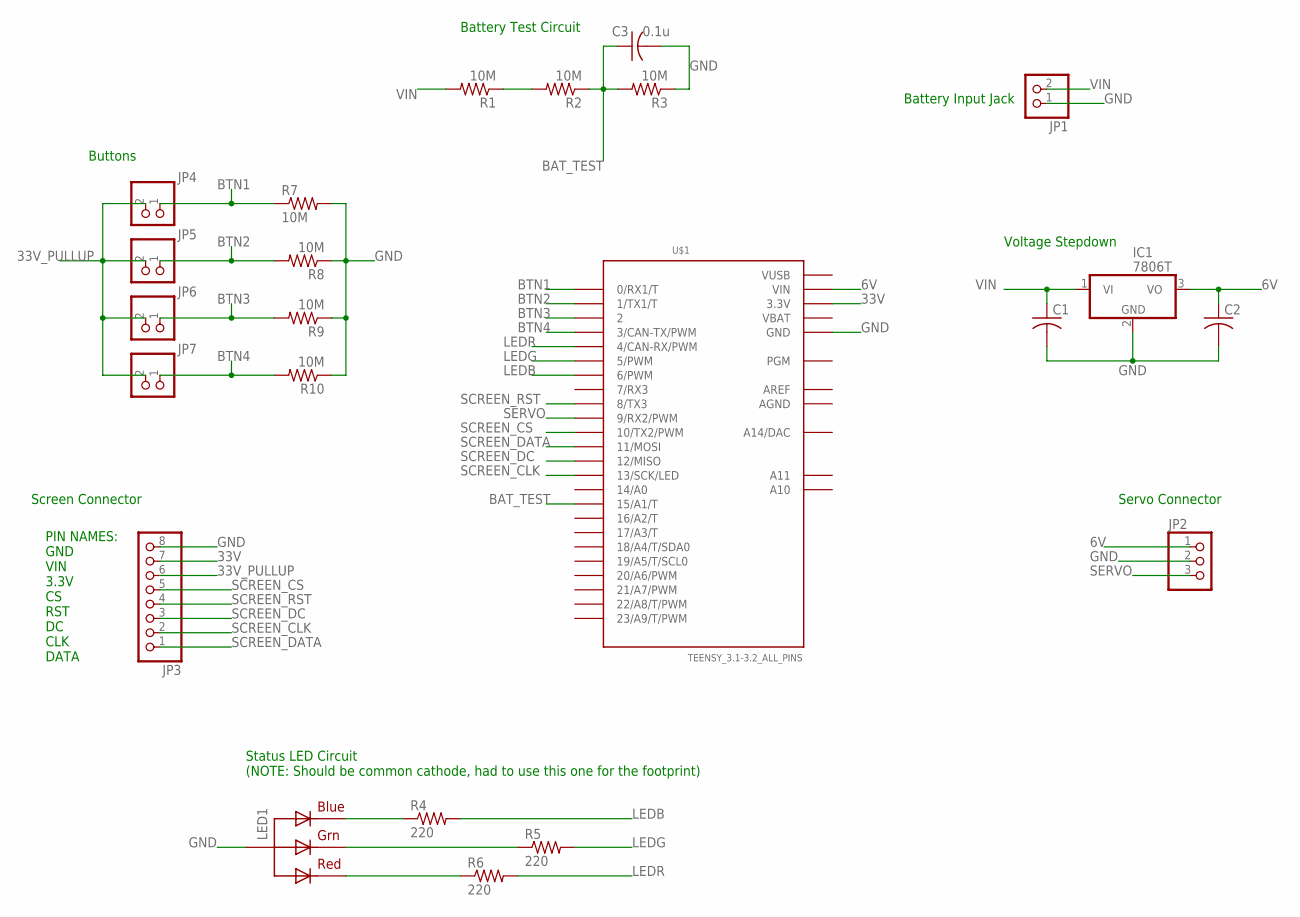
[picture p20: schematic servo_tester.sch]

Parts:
C1, C2: C-US050-024X044; C050-024X044
C3: 0.1u; C050-024X044
IC1: 7806T; TO220H
JP1, JP4, JP5, JP6, JP7: HEADER-1X2ROUND; 1X02_ROUND
JP2: HEADER-1X3ROUND; 1X03_ROUND
JP3: HEADER-1X870MIL; 1X08_ROUND_70
LED1: RGBLED_CA-5MM; LED5MMRGB
R1, R2, R3, R7, R8, R9, R10: 10M; 0204/5
R4, R5, R6: 220; 0204/5
U$1: TEENSY_3.1-3.2_ALL_PINS; TEENSY_3.0-3.2&LC_ALL_PINS

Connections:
6V: C2.1, IC1.3 (VO), JP2.1, U$1.VIN
33V: JP3.7, U$1.3.3V, U$1.3.3V1 (3.3V)
33V_PULLUP: JP3.6, JP4.2, JP5.2, JP6.2, JP7.2
AGND: U$1.AGND
AREF: U$1.AREF
BAT_TEST: C3.1, R2.1, R3.2, U$1.15/A1 (15/A1/T)
BTN1: JP4.1, R7.1, U$1.0 (0/RX1/T)
BTN2: JP5.1, R8.2, U$1.1 (1/TX1/T)
BTN3: JP6.1, R9.2, U$1.2
BTN4: JP7.1, R10.2, U$1.3 (3/CAN-TX/PWM)
GND: C1.2, C2.2, C3.2, IC1.2 (GND), JP1.1, JP2.2, JP3.8, LED1.2 (VCC), R3.1, R7.2, R8.1, R9.1, R10.1, U$1.GND, U$1.GND1 (GND)
LEDB: R4.2, U$1.6 (6/PWM)
LEDG: R5.2, U$1.5 (5/PWM)
LEDR: R6.2, U$1.4 (4/CAN-RX/PWM)
unnamed: LED1.1 (RED), R6.1
unnamed: LED1.4 (BLUE), R4.1
unnamed: LED1.3 (GREEN), R5.1
unnamed: R1.1, R2.2
SCREEN_CLK: JP3.2, U$1.13 (13/SCK/LED)
SCREEN_CS: JP3.5, U$1.10 (10/TX2/PWM)
SCREEN_DATA: JP3.1, U$1.11 (11/MOSI)
SCREEN_DC: JP3.3, U$1.12 (12/MISO)
SCREEN_RST: JP3.4, U$1.8 (8/TX3)
SERVO: JP2.3, U$1.9 (9/RX2/PWM)
VBAT: U$1.VBAT
VIN: C1.1, IC1.1 (VI), JP1.2, R1.2
VUSB: U$1.VUSB

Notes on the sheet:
PIN NAMES: GND VIN 3.3V CS RST DC CLK DATA
Battery Input Jack
Battery Test Circuit
Voltage Stepdown
Servo Connector
Status LED Circuit (NOTE: Should be common cathode, had to use this one for the footprint)
Screen Connector
Buttons

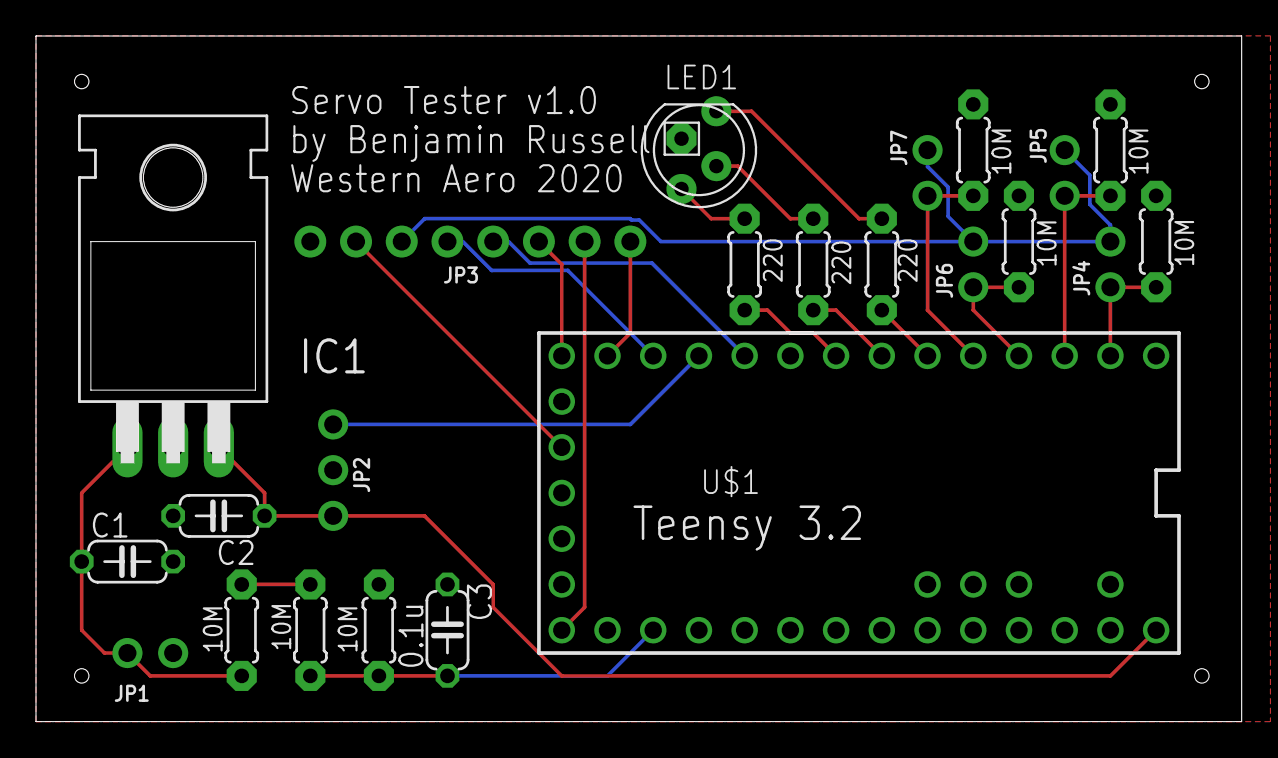
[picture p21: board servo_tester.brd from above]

Board: 2 copper layers, 67.0 x 38.1 mm, 23 parts (0 on the bottom side), 23 nets.

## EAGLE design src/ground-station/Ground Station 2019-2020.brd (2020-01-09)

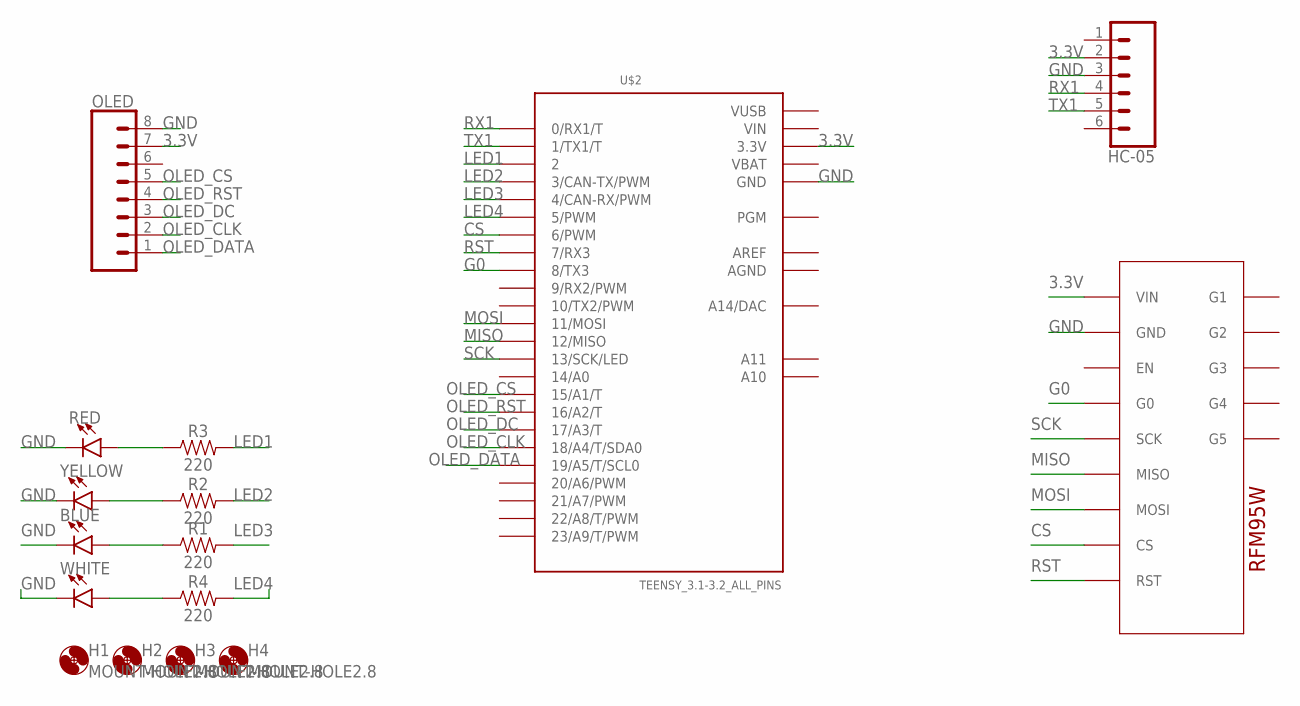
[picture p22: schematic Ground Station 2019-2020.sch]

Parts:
BLUE: LED5MM; LED_5MM
H1, H2, H3, H4: MOUNT-HOLE2.8; 2,8
HC-05: CONN_06SILK_FEMALE_PTH; 1X06
OLED: CONN_08"; 1X08
R1, R2, R3, R4: 220; AXIAL-0.3
RED: LED5MM; LED_5MM
U1: ADAFRUIT_RFM95W_LORA_RADIO
U$2: TEENSY_3.1-3.2_ALL_PINS; TEENSY_3.0-3.2&LC_ALL_PINS
WHITE: LED5MM; LED_5MM
YELLOW: LED5MM; LED_5MM

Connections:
3.3V: HC-05.2, OLED.7, U1.1 (VIN), U$2.3.3V, U$2.3.3V1 (3.3V)
AGND: U$2.AGND
AREF: U$2.AREF
CS: U1.8 (CS), U$2.6 (6/PWM)
G0: U1.4 (G0), U$2.8 (8/TX3)
GND: BLUE.K (C), HC-05.3, OLED.8, RED.K (C), U1.2 (GND), U$2.GND, U$2.GND1 (GND), WHITE.K (C), YELLOW.K (C)
LED1: R3.P$2 (2), U$2.2
LED2: R2.P$2 (2), U$2.3 (3/CAN-TX/PWM)
LED3: R1.P$2 (2), U$2.4 (4/CAN-RX/PWM)
LED4: R4.P$2 (2), U$2.5 (5/PWM)
MISO: U1.6 (MISO), U$2.12 (12/MISO)
MOSI: U1.7 (MOSI), U$2.11 (11/MOSI)
unnamed: BLUE.A, R1.P$1 (1)
unnamed: R2.P$1 (1), YELLOW.A
unnamed: R3.P$1 (1), RED.A
unnamed: R4.P$1 (1), WHITE.A
OLED_CLK: OLED.2, U$2.18/A4 (18/A4/T/SDA0)
OLED_CS: OLED.5, U$2.15/A1 (15/A1/T)
OLED_DATA: OLED.1, U$2.19/A5 (19/A5/T/SCL0)
OLED_DC: OLED.3, U$2.17/A3 (17/A3/T)
OLED_RST: OLED.4, U$2.16/A2 (16/A2/T)
RST: U1.9 (RST), U$2.7 (7/RX3)
RX1: HC-05.4, U$2.0 (0/RX1/T)
SCK: U1.5 (SCK), U$2.13 (13/SCK/LED)
TX1: HC-05.5, U$2.1 (1/TX1/T)
VBAT: U$2.VBAT
VIN: U$2.VIN
VUSB: U$2.VUSB

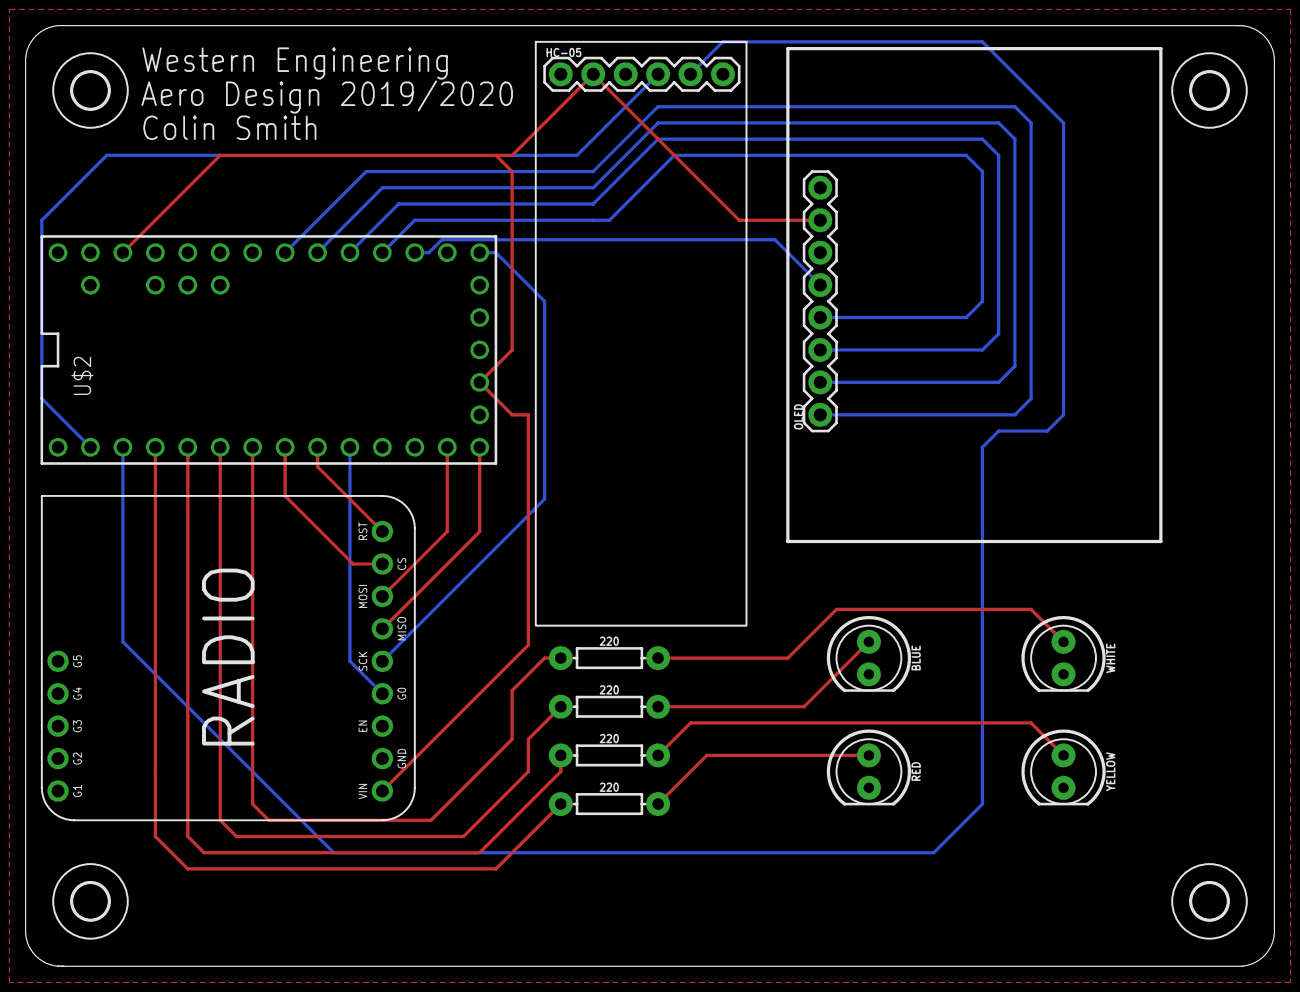
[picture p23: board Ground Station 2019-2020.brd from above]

Board: 2 copper layers, 97.8 x 73.7 mm, 16 parts (0 on the bottom side), 23 nets.

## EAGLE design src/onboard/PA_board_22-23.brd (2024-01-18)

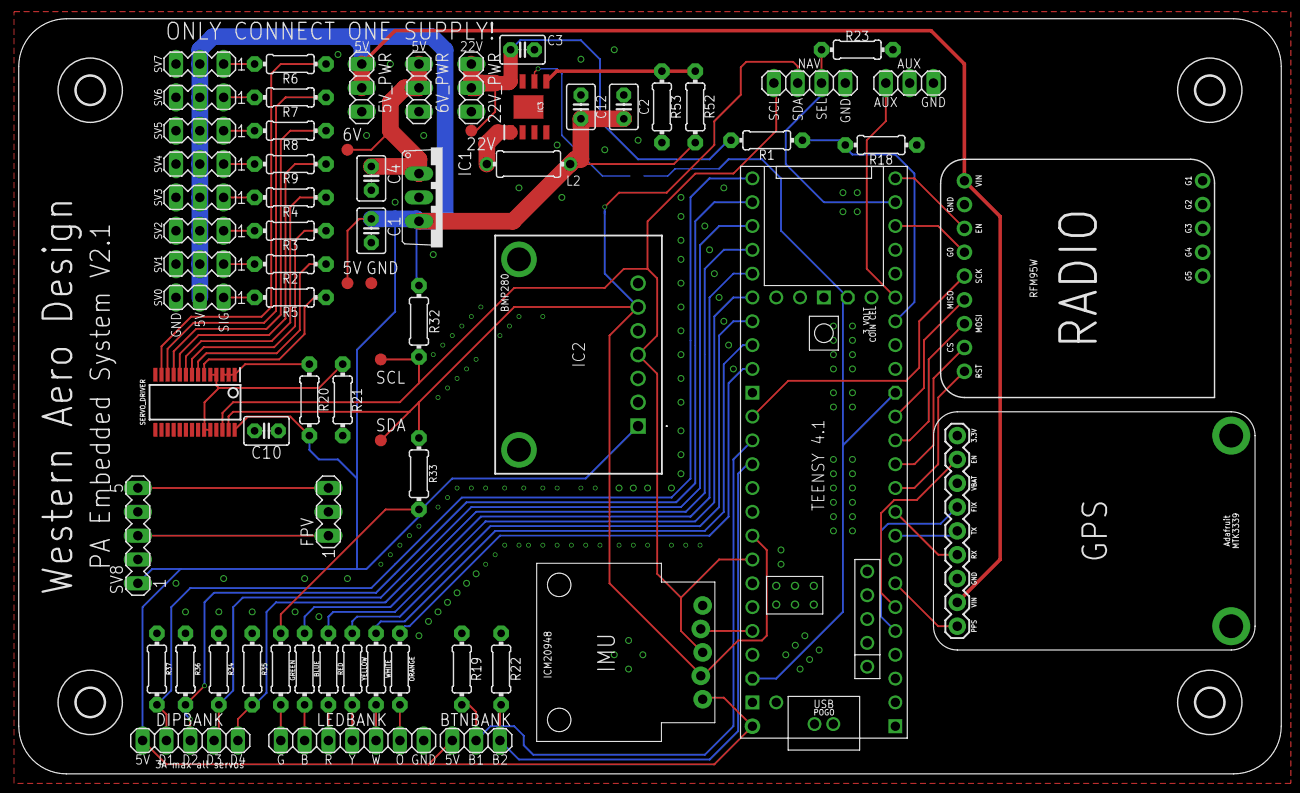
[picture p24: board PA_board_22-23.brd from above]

Board: 2 copper layers, 134.6 x 80.5 mm, 73 parts (1 on the bottom side), 62 nets.

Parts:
5V, 6V, 22V: PTR1B1,27; B1,27
5V_PWR: 5V_PWR; 1X03
6V_PWR: 6V_PWR; 1X03
22V_PWR: 22V_PWR; 1X03
AUX: 1X03
BLUE: 80; 0204/7
BTNBANK: 1X03
C1, C2, C3, C4, C10: 10uF; C2.5-3
C12: 470uF; C2.5-3
DIPBANK: 1X05
FPV: MA03-1
GND: PTR1B1,27; B1,27
GPSMTK3339: ADAFRUIT_MTK3339_GPS
GREEN: 150; 0204/7
IC1: MIC29310-5.0BT; TO220V
IC2: ADAFRUIT_BMP280; ADAFRUITBMP280
IC3: A5975D; SOIC127P600X170-9N
IMU: ICM20948BREAKOUTDEVICE; ICM20948BREAKOUT
L2: 27uH; TFI0307
LEDBANK: 1X07
NAV: 1X04
ORANGE: 150; 0204/7
R1: 1.8M; 0204/7
R2, R3, R4, R5, R6, R7, R8, R9: 220; 0204/7
R18: 430k; 0204/7
R19, R22, R23, R34, R35, R36, R37: 2.2k; 0204/7
R20, R21: 10K; 0204/7
R32, R33: 4.7k; 0204/7
R52: 1k; 0204/7
R53: 3k; 0204/7
RADIO: ADAFRUIT_RFM95W_LORA_RADIO
RED: 150; 0204/7
SCL: PTR1B1,27; B1,27
SDA: PTR1B1,27; B1,27
SERVO_DRIVER: PCA9685PW,112; SOP65P640X110-28N
SJ1: SJ
SV0, SV1, SV2, SV3, SV4, SV5, SV6, SV7: MA03-1
SV8: MA05-1
TEENSY4.1: TEENSY41
U$1, U$2, U$3, U$4: 3,0
WHITE: 90; 0204/7
YELLOW: 150; 0204/7

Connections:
3.3V: SJ1.2, TEENSY4.1.3V3-1, TEENSY4.1.3V3-2, TEENSY4.1.3V3-3
5V: 5V.TP, 5V_PWR.1, 5V_PWR.2, BTNBANK.3, C1.1, C2.1, C10.1, C12.1, DIPBANK.5, FPV.1, GPSMTK3339.VIN, GREEN.1, IC1.3, IC2.1, IMU.2-6V, L2.1, R20.2, R32.2, R33.2, R52.2, RADIO.1, SERVO_DRIVER.28, SV0.2, SV1.2, SV2.2, SV3.2, SV4.2, SV5.2, SV6.2, SV7.2, SV8.1, SV8.3, TEENSY4.1.VIN
6V: 6V.TP, 6V_PWR.1, 6V_PWR.2, C4.1, IC1.1
22V_INPUT: 22V.TP, 22V_PWR.1, 22V_PWR.2, C3.1, IC3.8, R1.2
AUX: AUX.3, TEENSY4.1.27-A13/SCK1
BATLEVEL: R1.1, R18.2, TEENSY4.1.26-A12/MOSI1
BLUE: BLUE.2, LEDBANK.6
BTN1: BTNBANK.2, R19.2, TEENSY4.1.14-A0/TX3/SPDIF_OUT
BTN2: BTNBANK.1, R22.2, TEENSY4.1.15-A1/RX3/SPDIF_IN
B_LED: BLUE.1, TEENSY4.1.37-PWM
CS0: RADIO.8, TEENSY4.1.10-CS\MQSR
DIP1: DIPBANK.4, R37.2, TEENSY4.1.33-MCLK2
DIP2: DIPBANK.3, R36.2, TEENSY4.1.34-RX8
DIP3: DIPBANK.2, R34.2, TEENSY4.1.35-TX8
DIP4: DIPBANK.1, R35.2, TEENSY4.1.36-PWM
GND: 5V_PWR.3, 6V_PWR.3, 22V_PWR.3, AUX.1, C1.2, C2.2, C3.2, C4.2, C10.2, C12.2, FPV.2, GND.TP, GPSMTK3339.GND, IC1.2, IC2.3, IC3.3, IC3.7, IMU.GND, LEDBANK.1, NAV.1, R18.1, R19.1, R21.1, R22.1, R23.1, R34.1, R35.1, R36.1, R37.1, R53.1, RADIO.2, SERVO_DRIVER.14, SERVO_DRIVER.25, SV0.3, SV1.3, SV2.3, SV3.3, SV4.3, SV5.3, SV6.3, SV7.3, SV8.2, SV8.4, TEENSY4.1.GND1, TEENSY4.1.GND2, TEENSY4.1.GND3, TEENSY4.1.GND4, TEENSY4.1.GND5, TEENSY4.1.GND6
GNDADDRESS: R21.2, SERVO_DRIVER.4, SERVO_DRIVER.5, SERVO_DRIVER.23, SERVO_DRIVER.24
GPS_EN: GPSMTK3339.EN, TEENSY4.1.4-BCLK2
GPS_FIX: GPSMTK3339.FIX, TEENSY4.1.3-LRCLK2
GPS_PPS: GPSMTK3339.PPS, TEENSY4.1.5-IN2
GREEN: GREEN.2, LEDBANK.7
IMU_INT: IMU.INT, TEENSY4.1.22-A8/CTX1
MISO0: RADIO.6, TEENSY4.1.12-MISO/MQSL
MOSI0: RADIO.7, TEENSY4.1.11-MOSI/CTX1
unnamed: R20.1, SERVO_DRIVER.1, SERVO_DRIVER.2, SERVO_DRIVER.3
unnamed: IC3.6, SJ1.1
unnamed: IC3.1, L2.2
unnamed: IC3.5, R52.1, R53.2
unnamed: R6.2, SV7.1
unnamed: R4.2, SV3.1
unnamed: R3.2, SV2.1
unnamed: R7.2, SV6.1
unnamed: R2.2, SV1.1
unnamed: R5.2, SV0.1
unnamed: R9.2, SV4.1
unnamed: R8.2, SV5.1
ORANGE: LEDBANK.2, ORANGE.2
O_LED: ORANGE.1, TEENSY4.1.41-A17/MISO1
PWM0: R5.1, SERVO_DRIVER.6
PWM1: R2.1, SERVO_DRIVER.7
PWM2: R3.1, SERVO_DRIVER.8
PWM3: R4.1, SERVO_DRIVER.9
PWM4: R9.1, SERVO_DRIVER.10
PWM5: R8.1, SERVO_DRIVER.11
PWM6: R7.1, SERVO_DRIVER.12
PWM7: R6.1, SERVO_DRIVER.13
RADIO_EN: RADIO.3, TEENSY4.1.32-OUT1B
RADIO_INT: RADIO.4, TEENSY4.1.30-CRX3
RADIO_RST: RADIO.9, TEENSY4.1.9-OUT1C
RED: LEDBANK.5, RED.2
RX2: GPSMTK3339.TX, TEENSY4.1.7-RX2/OUT1A
R_LED: RED.1, TEENSY4.1.38-A14/CS/IN1
SCK0: RADIO.5, TEENSY4.1.13-SCK/LED
SCL: IC2.4, IMU.SCL, NAV.4, R32.1, SCL.TP, SERVO_DRIVER.26, TEENSY4.1.19-A5/SCL0
SDA: IC2.6, IMU.SDA, NAV.3, R33.1, SDA.TP, SERVO_DRIVER.27, TEENSY4.1.18-A4/SDA0
SELECT_PIN: NAV.2, R23.2, TEENSY4.1.31-CTX3
TX2: GPSMTK3339.RX, TEENSY4.1.8-TX2/IN1
VIDEO: FPV.3, SV8.5
WHITE: LEDBANK.3, WHITE.2
W_LED: TEENSY4.1.40-A16/CS1, WHITE.1
YELLOW: LEDBANK.4, YELLOW.2
Y_LED: TEENSY4.1.39-A15/CS/OUT1A, YELLOW.1

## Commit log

2019-07-11 First Draft. All components on schematic and board. No routing completed.
    [Western Aero 2020.brd, Western Aero 2020.sch]
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2019-07-18 Reconfigured components, hid resistors and cut space
    [Western Aero 2020.brd]
2019-07-25 Added screwholes, adjusted addresses, few other tweaks
    [Western Aero 2020.brd, Western Aero 2020.sch]
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2019-08-18 Add new voltage regulator
    [Western Aero 2020.brd, Western Aero 2020.sch, part_order_digikey.xlsx]
2019-08-23 Changed test point parts. Updated parts list. Adjusted board layout.
    [Western Aero 2020.brd, Western Aero 2020.sch, part_order_digikey.xlsx]
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2019-10-09 Trace rework
    [Western Aero 2020.brd, Western Aero 2020.sch]
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2019-10-17 UBEC now supplies 6v with a 5v reg for onboard systems
    [Western Aero 2020.brd, Western Aero 2020.sch]
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2019-10-17 Update mounting hole placement
    [Western Aero 2020.brd]
2019-10-30 Added groundstation board and schematic files into separate folder. Also placed onboard circuit files in its own folder.
    [Ground Station 2019-2020.brd, Ground Station 2019-2020.sch, Western Aero 2020.brd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]
2019-11-21 Schematic and first routing attempt completed.
    [Ground Station 2019-2020.brd, Ground Station 2019-2020.sch]
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2020-01-05 Added LCD to board and increased space to accomidate
    [Ground Station 2019-2020.brd, Ground Station 2019-2020.sch]
2020-01-06 pushing servo tester board
    having sourcetree issues, uploaded through webpage
    [Servo_tester_rev1.brd, Servo_tester_rev1.sch]
2020-01-09 Added additional LCD, mounting holes and slik screen.
    [Ground Station 2019-2020.brd, Ground Station 2019-2020.sch]
2020-01-09 Fixed some connections and upgraded to ver 2.0
    [Ground Station 2019-2020.brd, Ground Station 2019-2020.sch, Servo_tester_rev1.brd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]
2020-01-09 Added pulldown resistors, mounting holes, and text
    [Servo_tester_rev1.brd]
2020-01-09 Added larger mounting holes and cleaned up silk screen
    [Western Aero 2020.brd]
2020-01-09 Fixed discrepancy between brd and sch, corrected pulldowns
    [Servo_tester_rev1.brd, Servo_tester_rev1.sch]
2020-01-09 Changed LCD to OLED display, changed mounting holes.
    [Ground Station 2019-2020.brd, Ground Station 2019-2020.sch]
2020-01-09 fixed DRCs and made smaller
    also added copper fill
    [Servo_tester_rev1.brd, Servo_tester_rev1.sch]
2020-01-09 fixed silkscreen
    [Servo_tester_rev1.brd]
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2020-01-21 Moved led to unblock usb port, tidied up buttons
    [Servo_tester_rev1.brd, Servo_tester_rev1.sch]
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2021-02-03 Reorganized 2019 and 2020 files into its own folder. Adding 2020/2021 board schematic and board layout of both main Teensy and navigation Teensy.
    [FinalSchematic1.0.brd, FinalSchematic1.0.sch, Navigationmark1.brd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]
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2021-02-20 Removed old board and schematic. Replaced with the new and larger board and schematic. Also updated the photos of both.
    [FinalSchematic1.1.brd, FinalSchematic1.1.sch]
2021-02-20 Removing the old schematic and board. (1.0 files)
    [FinalSchematic1.0-Bigger.brd, FinalSchematic1.0.brd, FinalSchematic1.0.sch]
2021-02-20 Rounded corners of navigation board. Made corner radius same on both boards.
    [FinalSchematic1.1.brd, Navigationmark1.brd]
2021-02-24 Updated board using the jlcpcb2layer.dru file for DRC check. Added names next to pinheaders. Adjusted silkscreen of component names. Updated photos of baord and schematic.
    [FinalSchematic1.2.brd, FinalSchematic1.2.sch, Navigationmark1.1.brd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]
2021-02-24 Changed Pinheader side names to Tplace on both boards
    [FinalSchematic1.2.brd, Navigationmark1.1.brd]
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2021-02-25 Removed 5V lines as one layer is a 5V pour so they were not needed because the components are through hole. Then updated photos of both boards
    [FinalSchematic1.2.brd, Navigationmark1.1.brd]
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2021-02-26 Changed hole sizes for both board to 3mm for M3 screws and made boards slilghtly larger to have room around the holes without disrupting the wire traces. Updated photos of both boards.
    [FinalSchematic1.2.brd, Navigationmark1.1.brd]
2021-02-26 Removed leftover wire trace on main board.
    [FinalSchematic1.2.brd]
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2022-02-07 Added button connection, rewired radio, removed pitot tube, split into pages
    [FinalSchematic1.2.brd, FinalSchematic1.2.sch]
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2022-02-09 Added button wires and fixed 5v input
    [FinalSchematic1.2.brd, FinalSchematic1.2.sch]
2022-02-09 Added 6v->5v LDO regulator
    [FinalSchematic1.2.brd, FinalSchematic1.2.sch]
2022-02-09 Added pulldown on select pin and added wiring for aux pin
    [FinalSchematic1.2.brd, FinalSchematic1.2.sch]
2022-02-09 Formatting changes and 6v test point
    [FinalSchematic1.2.brd, FinalSchematic1.2.sch]
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2022-02-13 Added BMP280 I2C Part
    Added to SCH sheet 4
    [FinalSchematic1.2.brd, FinalSchematic1.2.sch]
2022-02-13 Switched 6v LDO to MIC29310-5.0BT
    [FinalSchematic1.2.brd, FinalSchematic1.2.sch]
2022-02-13 Removed old schematic, moved current schematic up a level
    [FinalSchematic1.2.brd, FinalSchematic1.2.sch, Navigationmark1.1.brd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]
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2022-02-14 Rewired pins for easier routing
    [FinalSchematic1.2.brd, FinalSchematic1.2.sch]
2022-02-22 Added new BMP280 component to onboard
    [FinalSchematic1.2.brd, FinalSchematic1.2.sch]
2022-02-23 First routing attempt Still need to fix silkscreen
    [FinalSchematic1.2.brd, FinalSchematic1.2.sch]
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2022-02-23 Renamed main board files
    [MainBoard1.3.brd, MainBoard1.3.sch]
2022-02-27 Added gnd test point
    [MainBoard1.3.brd, MainBoard1.3.sch]
2022-03-01 Performed ERC and made changes
    [MainBoard1.3.brd, MainBoard1.3.sch]
2022-03-01 Updated BMP 280 VIN pin to be IO
    [MainBoard1.3.brd, MainBoard1.3.sch]
2022-03-01 Moved power supply silkscreen for visibility
    [MainBoard1.3.brd]
2022-03-02 Approved ERC warnings for header connections
    [MainBoard1.3.brd, MainBoard1.3.sch]
2022-03-02 Modified silkscreen and generated Gerbers
    [MainBoard1.3.brd]
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2024-01-18 added 2022/2023 PA board and changes to current gnd station board
    [MainBoard1.3.brd, PA_board_22-23.brd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]

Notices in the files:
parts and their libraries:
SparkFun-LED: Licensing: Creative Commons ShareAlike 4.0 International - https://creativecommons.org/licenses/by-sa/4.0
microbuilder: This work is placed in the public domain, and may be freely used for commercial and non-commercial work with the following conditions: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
